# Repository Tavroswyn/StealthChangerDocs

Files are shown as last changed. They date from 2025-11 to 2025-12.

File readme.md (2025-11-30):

# DraftShift Documentation Source

This repository contains the source code for the DraftShift documentation website.

Visit [https://draftshift.github.io/Docs](https://draftshift.github.io/Docs) for the actual documentation.

---

## Contributing

We welcome contributions! If you'd like to help improve the documentation:

- Submit a descriptive [pull request](https://docs.github.com/en/pull-requests/collaborating-with-pull-requests/proposing-changes-to-your-work-with-pull-requests/creating-a-pull-request) of the feature/issue you are addressing.

- Keep the documented information concise.

### Contributing Build Guides

If you want to contribute build guides, please refer to the [Build Guide documentation](CONTRIBUTING_GUIDES.md) for more information.

### Development Setup

To run the documentation site locally:

1. **Prerequisites**: Ensure Python is installed and included in your environment PATH.

2. **Install dependencies**:
   ```
   pip install -r requirements.txt
   ```

3. **Run the development server**:
   ```
   python -m mkdocs serve
   ```

The site will be available at `http://127.0.0.1:8000` with live reload enabled.

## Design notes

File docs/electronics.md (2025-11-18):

---
search:
  boost: 2 
---

{%- macro set_io_display(io) -%}
<span style="text-align: left;">
{%- if io is mapping -%}
{%- for key, value in io.items() -%}
<div>{{ key }}: {{ value }}</div>
{%- endfor -%}
{%- else -%}
No
{%- endif -%}
</span>
{%- endmacro -%}

{% set board_data = {} %}

## Power Requirements
Adding more tools increases the power draw. The required wattage for your build will need to be calculated depending on the chosen hardware for each tool by the end user. 

!!! info "Wattage Calculation"
    See the following example of how one could calculate the wattage required for 6 tool heads.

    - Printing heater max output = `70W`
    - Printing fans - 3 total = `(0.1A * 3 fans) * 24V = 7.2W`
    - Resting heater output (30% of max for 5 tools) = `((70W / 100) * 30) * 5 tools = 105W`
    - Resting fans - 5 tools - `(0.1A * 24V) * 5 tools = 12W`
    - Extruder motors - 0.6A for 6 tools - `(0.6A * 24V) * 6 tools = 86W`

    6 tools with a 70w heater has resulted in `280W` total. This greatly exceeds the standard Voron 200W power supply without taking the rest of the system in to account and either an additional power supply is required to make up the difference or the standard power supply needs to be replaced with a larger wattage supply.

!!! danger "Unsure?"
    If you are unsure of your power requirements please reach out for help from the community via one of the social platforms. 

## Toolhead Boards
Each tool requires a toolhead board to go with it. With multiple tools, the wiring would become a nightmare to manage without them. See the below table for a list of boards and their features.

| Board | Image | Manufacturer | Protocol | Fan Outputs | Fan Voltage | Thermistor | RGB | Probe | Filament Sensor |
| :-: | :-: | :-: | :-: | :-: | :-: | :-: | :-: | :-: | :-: |
{% for manufacturer, boards in tool_boards.manufacturers.items() -%}
{% for board_key, data in boards.items() -%}
{% if data.features is defined -%}
{%- set target_attr = '' if data.external_link else '{: target="_blank"}' -%}
| [{{data.name}}]({{data.product_url}}){{target_attr}} | <span style="width: 100px; display: block;">{{data.name}}</span> | {{ manufacturer }} | {{ data.features.protocol }} | {{ data.features.fans|string }} | {{ data.features.fan_voltage }} | {{ data.features.thermistor|string }} | {{ data.features.rgb|string }} | {{ data.features.probe|string }} | {{ data.features.filament_sensor|string }} | 
{% endif -%}
{%- endfor -%}
{%- endfor %}

## Distribution Boards
Distribution boards extend the amount of connections available that can be used to attach tool heads. They will be either extend your CAN network or will behave as a USB hub. Some boards also have an additional MCU that gan give you access to additional runout switches, thermistors, RGB, etc.

See below table of known boards for their protocol and capability:
!!! danger "TODO"
    Add images

| Board |  | Protocol | Outputs | IO |
| :-: | :-: | :-: | :-: | :-: |
{% for manufacturer, boards in distribution_boards.manufacturers.items() -%}
{%- for board_key, data in boards.items() -%}
{%- if data.features is defined -%}
{%- set target_attr = '' if data.external_link else '{: target="_blank"}' -%}
| [{{data.name}}]({{data.product_url}}){{target_attr}} | <span style="width: 100px; display: block;">{{data.name}}</span> | {{data.features.protocol}} | {{data.features.outputs}} | {{set_io_display(data.features.IO)}} | 
{% endif -%}
{%- endfor -%}
{%- endfor %}

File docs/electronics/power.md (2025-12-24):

## Requirements
Every toolchanger build is different, the end user must calculate the required power budget based on the specific hardware selected for each toolhead. This includes considering peak loads, simultaneous heating, and any auxiliary accessories. Ensuring that the power supply is sized with adequate overhead prevents instability and brownouts.

!!! example "Wattage Calculation"
    The following calculations are theoretical and are provided only as an example of how one might estimate the power requirements for a 6 tool build. Actual values may vary depending on the specific components, settings, and operating conditions of your build.

    - Toolheads - Active heater at max output = `70W`
    - Toolheads - Resting heater output (30% of max for 5 tools) = `((70W / 100) * 30) * 5 tools = 105W`
    - Toolheads - Active part cooling fans - 2 total = `(0.1A * 2 fans) * 24V = 4.8W`
    - Toolheads - Active hotend fans - 6 total = `(0.1A * 6 fans) * 24V = 14.4W`
    - Toolheads - Extruder motors - 0.6A for 6 tools - `(0.6A * 24V) * 6 tools = 86W`
    - Toolheads - combined total = `280,2W`  

    - Printer baseline = `120W`
    - Combined total = `400,2W`

In this example, 6 toolheads equipped with 70W heaters produce a combined load of 280W@24V. This alone exceeds the standard Voron 200W-24V power supply before accounting for motion stepper motors, electronics, fans, and other system components which would typically consume around 100-120W@24V.

So be safe and choose an adequately rated PSU for your expected current consumption.

!!! warning "Current Draw Baseline and Spikes"
    A standard Voron v2 draws somewhere in the 50-120w range "just sitting there" with all heaters and fans off, make sure you account for your baseline and spikes when you run the numbers for your power consumption.

!!! warning "DC Beds"
    A typical Voron has an AC bed, which does not draw power from the printer's PSU. If you have a DC bed, you will need to include that in your power calculations and spec the PSU accordingly.

In practice, this means that either an [additional power supply](#additional-power-supplies) would be required to cover the extra demand, or the stock supply must be [replaced with a higher-wattage unit](#replacement-power-supplies). These figures are illustrative; your actual power requirements will depend on the specific hardware and configuration of your build.

!!! danger "Unsure?"
    If you are unsure of your power requirements please reach out for help from the community via one of the social platforms. 

## Additional Power Supplies
A common method for increasing available power capacity is to add a second power supply unit (PSU) to the printer. While this approach is straightforward, it comes with both advantages and trade-offs:

- **Cost-effective:** Allows you to retain your existing PSU and supplement only the additional power required.
- **Increased space requirements:** A second PSU occupies additional room within the electronics bay.
- **Additional wiring complexity:** Integrating multiple PSUs introduces more wiring and requires careful planning to ensure safe, reliable operation.

!!! info "Common Ground"
    In multi-PSU systems, it is recommended to connect the negative (ground) rails together. This prevents floating grounds, which can lead to communication issues, inconsistent sensor readings, and other electrical irregularities.

!!! tip "48 Volt"
    If you’re adding another power supply and your motor drivers support it, incorporating a 48 V PSU can improve motion performance—particularly for Z-axis travel. Higher voltage reduces motor torque loss at speed, enabling faster and more responsive movement. Moving the load from all the motors to the 48V power supply frees up some capacity on the 24V power supply.

    Ultimately, upgrading to 48 V motion can shorten tool-change times and may be a worthwhile improvement depending on your hardware capabilities and performance goals.

## Replacement Power Supplies
Replacing your existing power supply unit (PSU) offers the inverse set of trade-offs compared to adding an [additional PSU](#additional-power-supplies). While it is generally the more expensive option, a single higher-capacity PSU can free up space in the electronics bay and reduce overall wiring complexity. Someone seeking a cleaner, more streamlined setup and prefers to avoid managing multiple power sources, a full PSU replacement may be the more appealing path.

## Power Supply Options
See the below table for some of the more common power supply unit (PSU) options. All PSUs are available in 24V and 48V options, unless noted otherwise.

{% for mf in power_supplies %}
### {{ mf }}
| Model | Wattage | Dimensions |
| :-: | :-: | :-: |
{%- for model, data in power_supplies[mf].items() %}
| {{ model }} | {{ data.wattage }} | {{ data.dimensions|join(", ") }}mm |
{%- endfor %}
{% endfor %}

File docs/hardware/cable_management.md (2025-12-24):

---
search:
  boost: 2 
---

## Umbilical Cables
An umbilical cable is required for each toolhead. It consists of a PTFE tube that feeds the filament to the toolhead's extruder, and an electrical wire that transfers power and data from the [distribution board](../electronics/distro_boards.md) to a [toolhead board](../electronics/th_boards.md). On a StealthChanger, keeping the tool's umbilical in a controlled state is extremely important. If a tool's umbilical were to obstruct any of the other tools, it could result in a crash and cause a print failure.

To help the umbilical move in a controlled fashion, we employ the use of a flat spring steel or piano wire. This addition gives the umbilical a controlled arc and helps it return to its resting position safely.

!!! tip "Spring Steel?"
    Flat spring steel (3x0.3mm) is the preferred aid for the tool's umbilical. It provides better lateral control and is what comes supplied as part of the LDO `Toolhead and Dock Kit`.

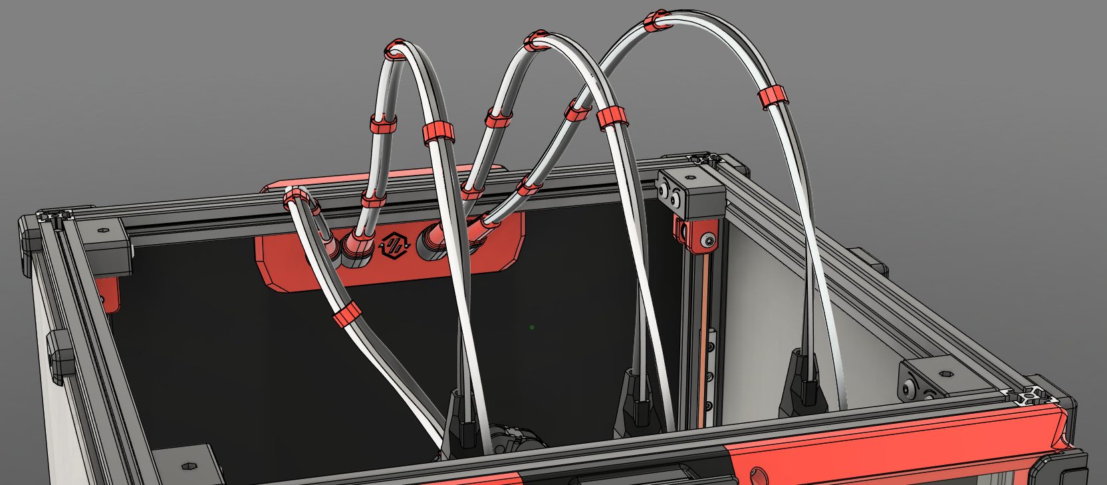
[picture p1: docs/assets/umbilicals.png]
Umbilical Cables


## Fanny Pack
Originally by [ManCheetah](https://www.printables.com/@EddieSha_454383){:target="_blank"}, the Fanny Pack has been adopted by DraftShift Design as the de facto method of housing a [distribution board](../electronics/distro_boards.md) on the rear of the printer. Compared to the original, our updated version brings compatibility with a number of [distribution boards](../electronics/distro_boards.md) and buck converter options.

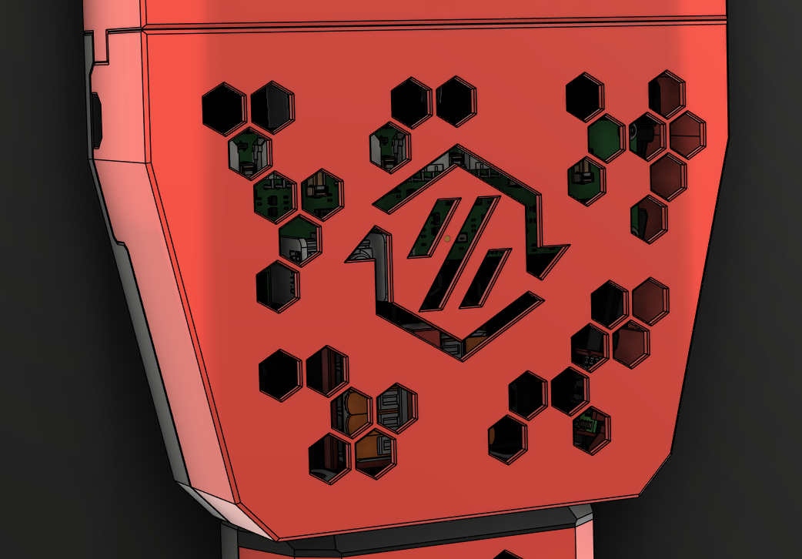
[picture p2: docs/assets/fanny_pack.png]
Fanny Pack


## Wire Duct
The Wire Duct serves as a conduit between the [Fanny Pack](#fanny-pack) and your printers electronics bay. Under its cover is an EMS compatible panel for you to mount any extra pieces you might need. 

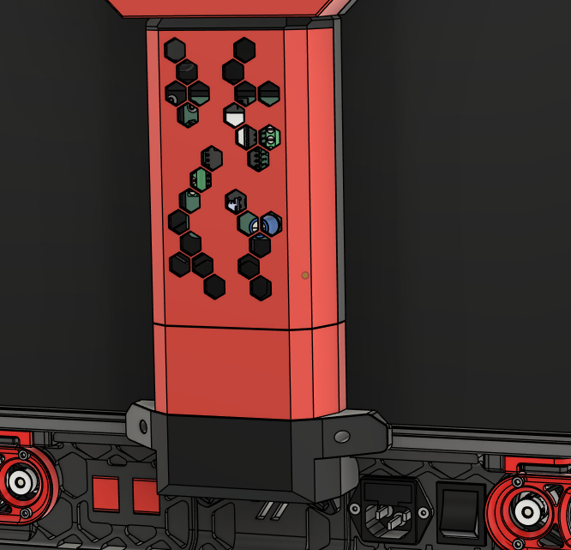
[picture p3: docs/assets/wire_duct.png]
Wire Duct


## Assembly
See the [Build Guides](../hardware/guides/cable_management/index.md) for assembly instructions.

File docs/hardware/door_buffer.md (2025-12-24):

---
search:
  boost: 2 
---

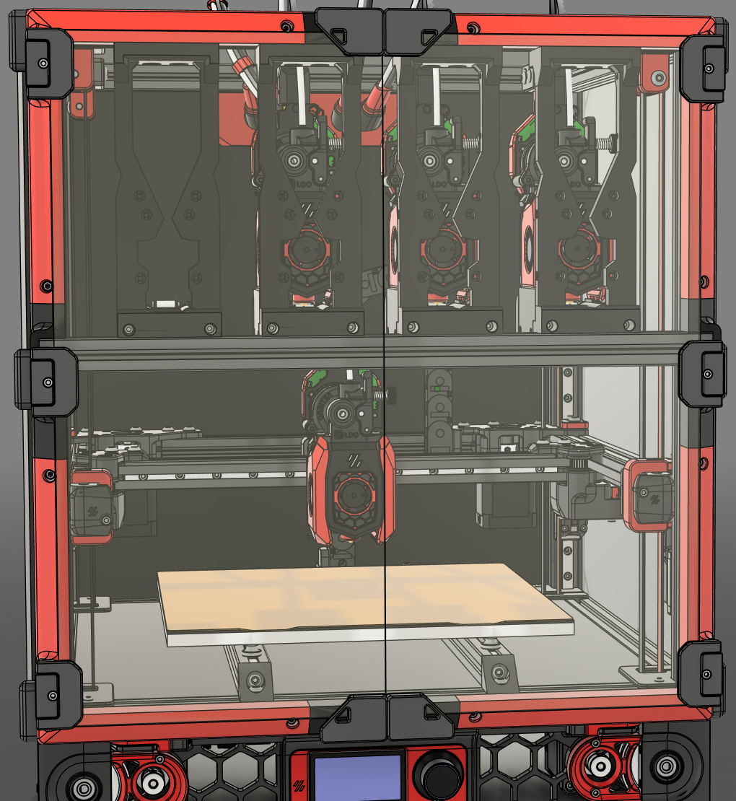
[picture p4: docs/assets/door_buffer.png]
Door Buffer


## Context

### The Problem
To give the [Modular Docks](modular_dock.md) the maximum amount of rigidity, they need to be supported above and below. Adding an extrusion [crossbar](#crossbar) solves that problem but also introduces another. With the crossbar in line with the frame, the standard Voron V2 front-idlers collide with the crossbar and moving the extrusion outside of the frame would get in the way of mounting the door.

Idler interference

### The Solution
Adding a Door Buffer provides a means to install the [crossbar](#crossbar) and retain the ability to mount the door on the front. The Door Buffer uses 3D printed pieces to fill the gaps around the front of the printers frame and adds new mounting points for the door.

Door buffer solution

There are versions of the Door Buffer for both [standard Voron V2 doors](https://github.com/DraftShift/DoorBuffer/tree/main/STL/Stock%20Voron){:target="_blank"} and the [ClickyClack Fridge Door Mod](https://github.com/DraftShift/DoorBuffer/tree/main/STL/Clicky-Klack){:target="_blank"}, as well as options for [Micron](https://github.com/DraftShift/DoorBuffer/tree/main/STL/Micron){:target="_blank"}.

!!! info "Alternatives"
    You don't necessarily need to use printed pieces to act as a buffer. There are some other methods that the community uses.

    * **2020/1515 Extrusion** - Using blind joints you can mount extrusion to the front of the frame essentially making it 4020/3015.
    * **4020/3015 Extrusion** - Build the front of your printers frame using larger extrusion. 
    * **Mini/Micro BFI** - [Mini/Micro BFI](https://github.com/DraftShift/StealthChanger/tree/main/UserMods/BT123/MiniBFI%20%2B%20MicroBFI){:target="_blank"} takes a different approach and shortens the BFI idlers. This means the [crossbar](#crossbar) can be kept within the printers frame at the cost of less printable area and reduces the amount you can adjust the A/B belts.

## Crossbar
The crossbar is a piece of extrusion mounted to the front of the printer’s frame, providing a rigid and stable attachment point for the bottom of the [Modular Dock](modular_dock.md).

The crossbar should be made from extrusion that matches your printer, 2020 for Voron V2 or 1515 for Micron. The length of the crossbar changes depending on the size of your frame and which version of Door Buffer you are using.

| Printer | DraftShift Crossbar | LDO Crossbar |
| --- | --- | --- |
| Voron 250 | 400mm | 370mm |
| Voron 300 | 450mm | 420mm |
| Voron 350 | 500mm | 470mm |
| Micron 180 | 302mm | - |

!!! tip "Crossbar Adapter"
    You can use the DraftShift Door Buffer with LDO length extrusions by using an [adapter](https://github.com/DraftShift/DoorBuffer/tree/main/STL/Adaptor){:target="_blank"}.

!!! info "Monolith AWD"
    With Monolith protrusion the front motors would hit the crossbar even with the door-buffer. To work around that you can use one of the following usermods:

    - [printed adapter for door buffer with crossbar and Monolith AWD](https://github.com/DraftShift/DoorBuffer/tree/main/UserMods/MikeYankeeOscarBeta/Doorbuffer_Adapters){:target="_blank"}
    
    - [printed adapter for crossbar with doomcube 4040 frame and Monolith AWD](https://github.com/DraftShift/ModularDock/tree/main/UserMods/MikeYankeeOscarBeta/Monolith_Crossbar){:target="_blank"}

## Assembly
The assembly guide for the Door Buffer can be found in the [Build Guides](guides/door_buffers/index.md) section.

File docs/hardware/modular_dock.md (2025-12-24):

---
search:
  boost: 2 
---

The Modular Dock gives you a place to rest the tools while they are not in use. Its modular design allows for flexible configurations to suit any printer and toolhead combination.

## Application
The Modular Dock can be used in a variety of ways. The most common and recommended way is to use it in combination with a [crossbar](door_buffer.md#crossbar). The [crossbar](door_buffer.md#crossbar) is a part of the [Door Buffer](door_buffer.md) and offers a sturdy mounting point for the dock to be supported both above by the frame and below by the [crossbar](door_buffer.md#crossbar).

Alternatively, the dock can be mounted to the printer's frame using the [Stabilizers](#stabilizers) and [Link](#links) components. This keeps the lower portion of the docks in place by joining them together while the outer docks get supported by the side of the printers frame. This adds some rigidity, but will not provide the same level of stability as the [crossbar](door_buffer.md#crossbar).

Finally, the docks can be hung from the top of the printers frame with no lower support. This is the least stable option and should only used when the other options are not available to you. If you choose to go for top-mounted docks it's recommended to mount extra corner brackets to avoid the top-extrusion twisting around the blind joints.

## Modularity
Because of its modularity, the Modular Dock has many differing pieces that can become overwhelming rather quickly. To help navigate the options, the modular dock is broken down into the following subcomponents:

* [Base](#base) - The section that the tool rests on while docked.
* [Blocker](#blocker) - A section that mounts inside the [base](#base) and blocks the nozzle while docked, helping with ooze control.
* [Back](#back) - Attaches to the rear of the [base](#base) to allow adjustment of the tools resting position.
* [Wiper](#wiper) - A means of wiping the nozzle as the toolhead is exiting the dock.
* [Frame](#frame) - The upright portion of the dock that connects to the top of the printer's frame and optionally a [crossbar](door_buffer.md#crossbar).
* [Links](#links) - Attaches to the bottom of the docks, increasing rigidity for hanging docks.
* [Stabilizers](#stabilizers) - Ties the docks in to the side of the frame, further increasing rigidity for hanging docks.
* [Containers](#containers) - An optional addon that add a bit of flair to the front of the dock.

## Components
### Base
The base is a large section that is toolhead specific which has been shaped to match the bottom of the toolhead. It defines the width of the dock and helps define the position that the tool sits in on the Y Axis. The base can be availiable in 2 variants, `standard` and `stubby`. Every toolhead has a `standard` base, but not all toolheads have the smaller `stubby` base.

!!! warning "Smaller is better right?"
    The `stubby` base is **NOT** compatible when using a [Door Buffer](door_buffer.md). If you are using a [Door Buffer](door_buffer.md), you MUST use the `standard` base. 

| Base - Standard | Base - Stubby |
| :-: | :-: |
| Standard | Stubby |

### Blocker
The Blocker is a section that is toolhead agnostic and mounts inside the [Base](#base). It serves as a barrier to prevent ooze while the tool is docked. It is availiable in 2 variants, `cup` and `spring steel`. 

There is no real advantage using one over the other, its more about what you have available to you.

The `cup` version uses a pen spring, screw and heatset insert, while the `spring steel` version uses a strip of flat spring steel. Both versions use high temperature RTV silicone to block the nozzle.

!!! tip "LDO Toolhead and Dock Kit"
    The LDO Toolhead and Dock Kit includes pre moulded `spring steel` blockers. If you are using the LDO kit, you will need to print the `spring steel` variant.

| Blocker - Cup | Blocker - Spring Steel |
| :-: | :-: |
| Cup | Spring Steel |

### Back
The Back plate is toolhead specific and bolts to the rear of the [Base](#base). Adjusting it up or down can help maintain the tool's alignment while it is docked.

| Back |
| :-: |
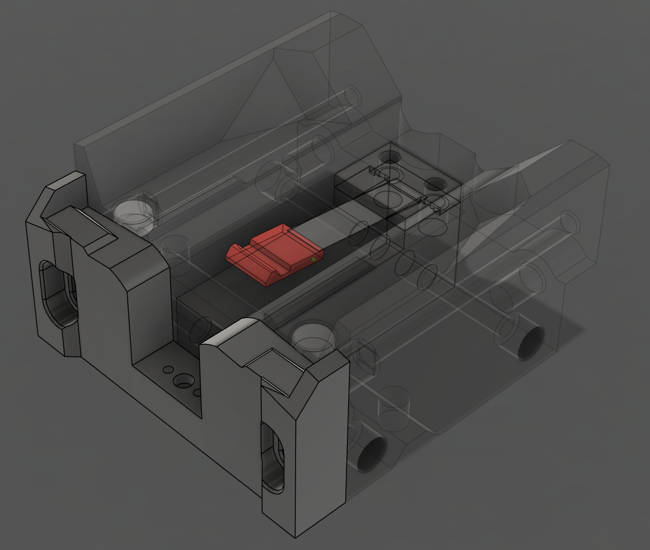
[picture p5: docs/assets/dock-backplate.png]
Back
|  |

### Wiper
The Wiper is toolhead agnostic and mounts to the [Back](#back) plate. There are 2 variants, `ptfe` and `bambu`. Both use a piece of PTFE tube to wipe the nozzle as it exits the dock. The `bambu` version emulates the wiper from the P1/X1 series of printers and can be printed or purchased from [BambuLab](https://bambulab.com){:target="_blank"}.

!!! tip "Wipers Are Considered Optional"
    If you get excess ooze while returning to the print, a wiper may help.

| Wiper - PTFE | Wiper - Bambu |
| :-: | :-: |
| PTFE | Bambu | -->

### Frame
The Modular Dock Frame can be considered to be the front of the dock. It consists of left, right, top and bottom pieces. 

The left and right pieces come in 2 variants, `standard` and `short`. This determines the height of the dock. 

!!! warning "Short Frame Saves More Space?"
    Using the `short` version of the Frame can give you more printable area under the bed, but it does have some caveats. 

    * You may need to adjust the position of the z rails to ensure the carriage can reach.
    * [StealthBurner](toolheads.md#stealthburner) is not compatible with short docks.
    * [Containers](#containers) are not compatible with short docks.

Versions of both the top and bottom pieces are available for 1515 and 2020 extrusions. Both of those versions have 2 variants, `standard` and `crossbar`. The `crossbar` versions are used in combination with [Door Buffer](door_buffer.md), which mounts an extrusion outside of the frame as a crossbar. The `standard` versions can be used for a crossbar in-line with the frame, as a combination with [Stabilizers](#stabilizers) or when hanging from the top of the printers frame. Optionally there is also an 'L bracket' that can help with stability of hanging docks.

| Standard Height | Short Height |
| :-: | :-: |
| Standard-Standard | Short-Standard |

### Links
Links can be used to tie the frame and base of the docks together to gain more rigidity for hanging docks or when using [Stabilizers](#stabilizers). There are seperate links pieces for the [Frame](#frame) and the [Base](#base).

The links for the [Frame](#frame) differ depending on whether 2020 or 1515 top and bottom pieces are used and whether the dock is for a wider tool or not. The links for the [Base](#base) are the same no matter the configuration.

| Links |
| :-: |
| Links |

### Stabilizers
Stabilizers can be added to the first and last dock to help with rigidity for hanging docks. There are left and right brackets for 2020 and 1515 frames which mount on the top Y axis extrusions of the printer's frame, spacers and a brace which connects to the outer docks.

!!! tip "Think ahead"
    * There are different versions of the brace depending on the combination of pieces chosen to build the dock. Make sure to get the correct version.
    * The spacers can be scaled in the slicer to adjust the offset of the docks from the side of the printer. These should be printed last, giving you a change to measure the distance you require.

| Stabilizers |
| :-: |
| Stabilizer |

### Containers
Containers are an aesthetic addon that can be position in the frame of the Modular Dock. They are considered optional.

| Containers |
| :-: |
| Containers |

## Assembly
The assembly guide for the Modular Dock can be found in the [Build Guides](guides/modular_docks/index.md) section. There you will find a guide for the different components and how to contruct the final assembly.

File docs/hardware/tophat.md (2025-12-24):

---
search:
  boost: 2 
---

## The Problem
While the tools are parked or when printing high up, the umbilical extends past the top of the printer. Most printers let the umbilical touch the top or go to the side. That is not an option for StealthChanger, the umbilical would interfere with other tools or their umbilical and could pull them from their dock. 

## The Solutions

### Extrusion Tophat
The Extrusion Tophat is like an extension of your printer. It uses the same extrusion and panel design as the printers frame. See the below table for a list of extrusion and panel sizes per printer size:

| Printer | Vertical Extrusion | Horizontal Extrusion | Panels |
| :-: | :-: | :-: | :-: |
| Voron 350 | 250mm x4 | 470mm x8 | 483x223x3mm x4 |
| Voron 300 | 200mm x4 | 420mm x8 | 433x173x3mm x4 |
| Voron 250 | 200mm x4 | 370mm x8 | 383x173x3mm x4 |
| Micron 180 | 150mm x4 | 280mm x8 | 290x130x3mm x4 |

Extrusion Tophat

!!! tip "LDO Kit"
    The hardware required for the Extrusion Tophat comes as part of LDO's `Tophat and Door Buffer Kit`.

### Printed Tophat
The Printed Tophat was developed for users that do not have easy access to aluminium extrusion or acrylic panels. The only additional hardware is screws, nuts and heat-set inserts.

Printed Tophat

!!! tip "Interim Tophat"
    Many of our members have fabricated a Tophat from cardboard which can be used while printing the pieces for your Printed Tophat.

### Do Nothing
If you plan on only printing open air, then you do not necessarily require a Tophat. You could just remove the top panel and let the umbilical cables extend past the top of the printer. 

## Assembly
The assembly guides for the Tophats can be found in the [Build Guides](guides/tophats/index.md) section.

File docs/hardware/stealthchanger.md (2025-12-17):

---
search:
  boost: 2 
---

StealthChanger is the key component and namesake of the StealthChanger ecosystem. It can be broken down in to 2 main components, the [Shuttle](#shuttle) and [Backplate](#backplate), which allows the toolhead to be removed from the gantry and be docked so that another tool can be picked up. During operation, the mechanism also behaves like [Voron Tap](https://github.com/VoronDesign/Voron-Tap){:target="_blank"} and can be used for probing the bed. The [Shuttle](#shuttle) and [Backplate](#backplate) completely replace Voron TAP hardware, only the optoTAP sensor is re-used.

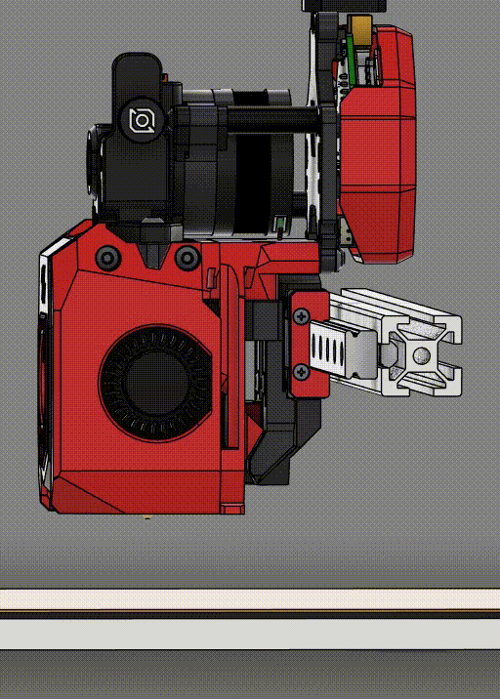
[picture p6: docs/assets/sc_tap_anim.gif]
StealthChanger
StealthChanger 

## Shuttle
The StealthChanger Shuttle gets mounted to the gantry's X-rail MGN carriage and serves the purpose of being a receptacle for the [Backplate](#backplate). It uses bushings and magnets which allow the [Backplate](#backplate) to
kinematically attach to the gantry.

### Printed vs CNC
The printed and CNC versions of the Shuttle both operate in the same way. You can print the shuttle and source the bushings, magnet and screws or purchase a ready to go CNC shuttle. 

CNC Shuttles offer some QOL improvements like improved belt retention and in the case of LDO's Shuttle, precision-machined bushings.

When printing a Shuttle, it is important to note that the selection of material you use and your printers accuracy are important. Please reference the [Print Tuning Section](../getting_started.md#print-tuning) before printing your Shuttle.

!!! warning "ABS+"
    We have found that when used for StealthChanger, ABS+ tends to crack over time and advise against using it.

Shuttles

| Shuttle | MGN12 | MGN9 | Micron | 6mm Belt | 9mm Belt |
| :-: | :-: | :-: | :-: | :-: | :-: |
| Printed | :fontawesome-solid-check:{style="color:green;"} | :fontawesome-solid-asterisk:{style="color:orange;"} | :fontawesome-solid-asterisk:{style="color:orange;"} | :fontawesome-solid-check:{style="color:green;"} | :fontawesome-solid-asterisk:{style="color:orange;"} |
| CNC | :fontawesome-solid-check:{style="color:green;"} | :fontawesome-solid-xmark:{style="color:red;"} | :fontawesome-solid-xmark:{style="color:red;"} | :fontawesome-solid-check:{style="color:green;"} | :fontawesome-solid-check:{style="color:green;"} |

!!! asterisk "MGN9/Micron"
    The hole spacing on MGN9 is too small to clamp the belts reliably without the screws getting in the way. This means a Voron V2 with MGN9 on X axis or a Micron requires the use of the [Shuttle Keeper](#shuttle-keeper). 

!!! asterisk "9mm belts"
    9mm belts can be used with CNC Shuttles. If you want to use 9mm belts with a printed Shuttle, a [usermod by BT123](https://github.com/DraftShift/StealthChanger/tree/main/UserMods/BT123/Split%20Keeper){:target="_blank"} is required.

!!! info "Monolith and Inverted Belts"
    Inverted belts with printed shuttle require the use of this [usermod by BT123](https://github.com/DraftShift/StealthChanger/tree/main/UserMods/BT123/Split%20Keeper){:target="_blank"}.
    Inverted belts can be mounted to CNC Shuttle as is, but with [Monolith](https://github.com/Monolith3D/Monolith_Gantry/tree/main){target="_blank"} this results in slight angled belt-path. To get a straight belt path with CNC-shuttle you can either use [belt-lock](https://github.com/MikeYankeeOscarBeta/belt_lock){:target="_blank"} or this [XY-joint mod by dderg](https://github.com/Monolith3D/Monolith_Gantry/tree/main/UserMods/dderg/XY%20Joints%20compatible%20with%20Fysetc%20CNC%20Stealthchanger%20Shuttle){:target="_blank"}.

## Shuttle Keeper
The Shuttle Keeper is an additional component that can be used to hold the belts in place while the [Shuttle](#shuttle) is removed from the MGN Rail. There are situational reasons as to when and why you would want to use a Shuttle Keeper. See the below list for details.

* Only compatible with a printed [Shuttle](#shuttle).
* Required for a MGN9 [Shuttle](#shuttle).
* Optional for a MGN12 [Shuttle](#shuttle).
* Shuttle Keeper moves the toolhead forward 5-6mm.

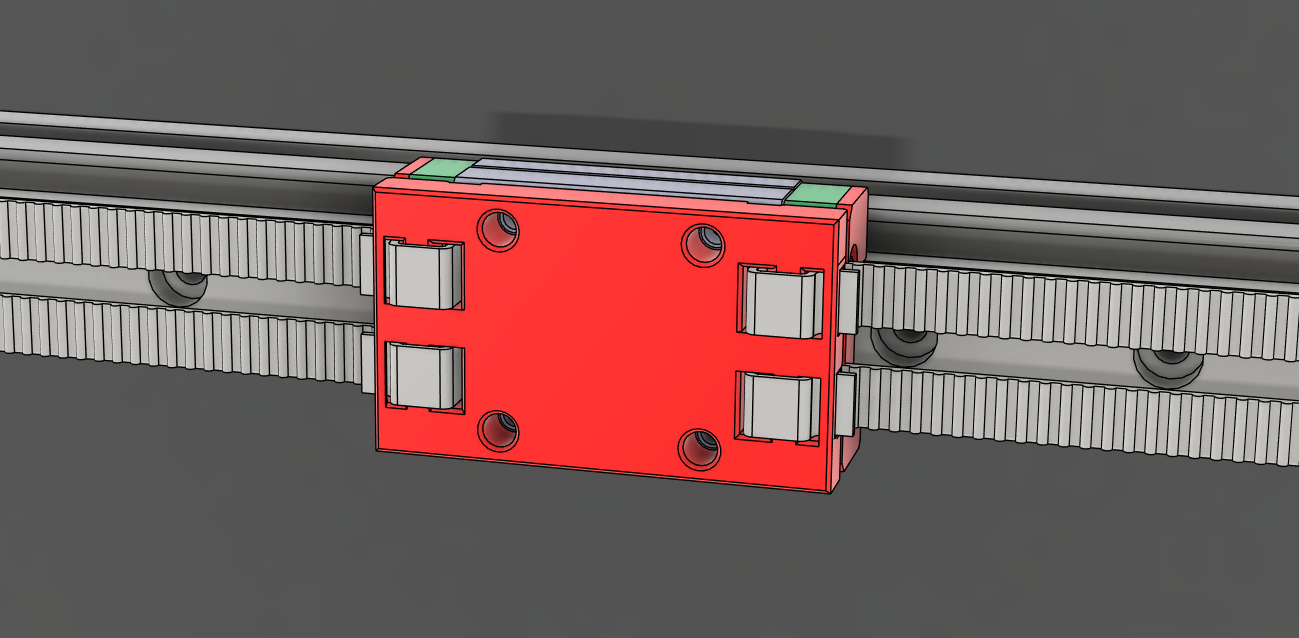
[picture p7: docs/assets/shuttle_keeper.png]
Shuttle Keeper


## Belt Helper
Belt helper is a tool that will hold your belts for you while installing the [Shuttle](#shuttle). Once attached to the belts, the Belt Helper will assist in pulling the belts into position for the [Shuttle](#shuttle) to clamp them.

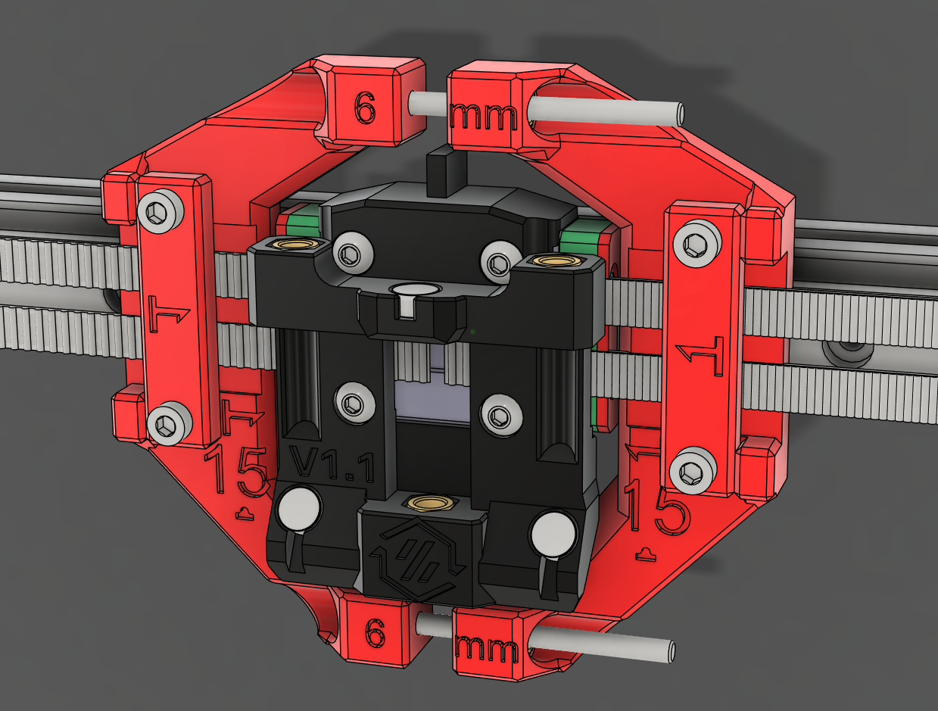
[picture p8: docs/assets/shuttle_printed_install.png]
Shuttle Install


!!! tip "One Tool to Rule Them All"
    The Belt Helper was designed to assist with installing the printed [Shuttle](#shuttle). It can also be useful with CNC shuttles to give you that extra set of hands you always wanted.

!!! info "Mini/Micro BFI"
    If using [Mini/Micro BFI](https://github.com/DraftShift/StealthChanger/tree/main/UserMods/BT123/MiniBFI%20%2B%20MicroBFI){:target="_blank"}, the Belt Helper is required to pre tension your belts to a point where your idlers only need minimal adjustment.

## Backplate
The StealthChanger Backplate is the companion component to the [Shuttle](#shuttle). Each compatible toolhead has its own unique Backplate that gets attached to the tool. The backplate is a critical component of StealthChanger and requires you to ensure you have good print accuracy, especially when pairing with a CNC Shuttle. Please reference the [Print Tuning Section](../getting_started.md#print-tuning) before printing your Backplate. For a list of compatible tools, see the [Toolheads](toolheads.md) page.

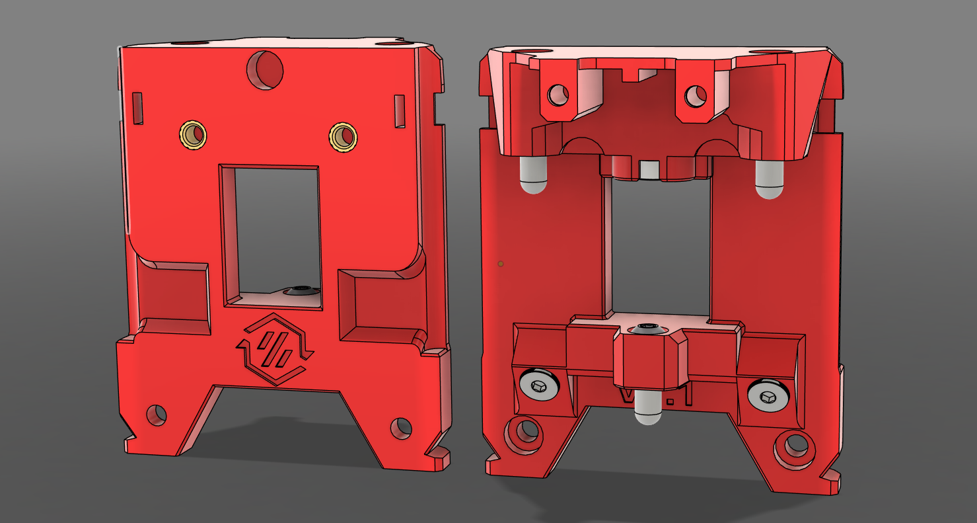
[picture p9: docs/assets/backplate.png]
Backplate


## Assembly
See the [Shuttle Build Guides](guides/shuttles/index.md) and [Backplate Build Guides](guides/backplates/index.md) sections for assembly instructions.

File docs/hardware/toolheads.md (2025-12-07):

For the purposes of StealthChanger the toolhead selection is rather important. It is often the deciding factor in how the rest of the build is configured. It determines which docks you can use, the maximum number of tools you can use, and can also have a large impact on power requirements.

???+ info "Printing"
    Officially supported toolheads require no modifications to operate with StealthChanger beyond the installation of the StealthChanger backplate and, where applicable, a spacer. Each toolhead can be sourced from their respective repositories. 
    
    Toolheads that require modification to work with StealthChanger are not officially supported and should be submitted as a usermod.

??? info "Extruders"
    * You can use any extruder you want as long as it is supported by the toolhead of your choice.
    * It's important to note that the width of the extruder may impact the maximum tool count as it may require a wider dock, limiting the total number of tools that can be accommodated.
    * :warning: Pay attention to the tensioning screw on the extruder, it may collide with the tool beside it if it extends outside the tool's width and there is not enough room between them.

??? info "Hotends"
    * Choose whichever hotend you like, as long as the toolhead supports it, you can use it.
    * :warning: Some high-flow hotends may require significant tuning to prevent oozing while moving to and from the dock.

??? tip "Community Recommendation"
    [Anthead](#anthead) is the recommended toolhead due to its integrated magnets in the fan ducts, which enhance stability during the docking process. Other tools can achieve similar results, but may require additional modifications.

    The LDO `Toolhead and Dock Kit` includes all necessary hardware for the [Anthead](#anthead), with the exception of the extruder and hotend components.

<div class="grid cards" style="text-align: center;" markdown>

{% for tool, tool_data in tools.toolheads.items() %}
    {% set v250 = tools.max_tools[tool_data.dock_width][250]|string if tools.max_tools[tool_data.dock_width][250] > 0  else '-' %}
    {% set v300 = tools.max_tools[tool_data.dock_width][300]|string if tools.max_tools[tool_data.dock_width][300] > 0  else '-' %}
    {% set v350 = tools.max_tools[tool_data.dock_width][350]|string if tools.max_tools[tool_data.dock_width][350] > 0  else '-' %}
    {% set m180 = tools.max_tools[tool_data.dock_width][180]|string if tools.max_tools[tool_data.dock_width][180] > 0  else '-' %}
-   <span id="{{ tool.replace(' ', '_').lower() }}"></span>

    ### {{ tool }}

    {{ tool }}

    **Author:** {{ tool_data.author }}

    **Dock Width:**{ title="Standard: 60mm<br>Wide: 76mm" } {{ tool_data.dock_width.capitalize() }}

    **Short Dock:**{ title="The height of the dock (Z axis) being less than standard. For Voron printers, the shorter height is not available for larger toolheads. Compatibility with Door Buffer varies depending on toolhead configuration. For Micron printers the short variant is a requirement." } {{ ':fontawesome-solid-check:{ style="color:green;" }' if tool_data.short_dock else ':fontawesome-solid-xmark:{ style="color:red;" }' }}

    **Stubby Dock:**{ title="The depth of the dock (Y axis) being less than standard and is not compatible with Door Buffer and is only available for the smaller toolheads." } {{ ':fontawesome-solid-check:{ style="color:green;" }' if tool_data.stubby_dock else ':fontawesome-solid-xmark:{ style="color:red;" }' }}

    {% if tool_data.extra is defined %}
    {% for extra in tool_data.extra %}
    {{ extra }}<br>
    {% endfor %}
    {% endif %}

    | Size | Max Tools |
    |--------------|------------|
    | 250mm Voron  | {{ v250 }} |
    | 300mm Voron  | {{ v300 }} |
    | 350mm Voron  | {{ v350 }} |
    | 180mm Micron | {{ m180 }} |

    [:fontawesome-brands-github: View on GitHub]({{ tool_data.url }}){:target="_blank" .md-button}

{% endfor %}

</div>

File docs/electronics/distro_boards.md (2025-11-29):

{%- macro set_io_display(io) -%}
{%- if io is mapping -%}
{% for key, value in io.items() %}
    **{{ key }}:** {{ value }}
{% endfor %}
{%- endif -%}
{%- endmacro -%}

Distribution boards expand the number of connections available for attaching toolheads. They can either extend your CAN network or function as a USB hub. Some distribution boards also include an additional MCU, providing access to extra inputs and outputs such as filament runout switches, thermistors, RGB lighting, and other peripherals.

??? tip "CAN Bus"
    For CAN bus communication, it is highly recommended to follow [Esoterical's CAN Bus Guide](https://canbus.esoterical.online/){target="_blank"}, which provides clear, step-by-step instructions for flashing and configuring the host computer, MCU and toolhead boards.

??? tip "USB"
    For USB communication it is recommended to use the manufacturer's documentation to guide you through flashing and configuring the distribution board.

<div class="grid cards" style="text-align: center;" markdown>
{% for manufacturer, boards in distribution_boards.manufacturers.items() %}
    {% for board, data in boards.items() %}
    {% if data.features is defined %}
    {% set target_attr = "_blank" if data.external_link else "" %}
-    ## {{ board }}
    
    {{ board }}
    
    **Manufacturer:** {{ manufacturer }}
    
    **Protocol:** {{ data.features.protocol }}
    
    **Outputs:** {{ data.features.outputs }}
    
    {{ set_io_display(data.features.IO) }}
    
    [:octicons-info-16:More Info]({{ data.url }}){:target="_blank" .md-button .md-button--primary} [:material-cart:]({{ data.product_url }}){:target="{{ target_attr }}" .md-button}
    {% endif %}
    {% endfor %}
{% endfor %}
</div>

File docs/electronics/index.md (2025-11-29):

# Power and Electronics

Building a toolchanger inherently increases both the [power demand](power.md) and the amount of I/O the printer must support. Each toolhead typically needs its own heater, extruder, fans, and OptoTap PCB, which quickly makes direct wiring complex and unwieldy.

The most effective way to manage this is to use a [toolhead board](th_boards.md) on each tool, which keeps all of the tool’s wiring self-contained within the toolhead itself. Complementing this, [distribution boards](distro_boards.md) serve as centralized hubs that deliver both power and data to each toolhead board, typically over CAN bus or USB. Together, these boards simplify wiring, improve reliability, and make multi-tool systems far easier to build and maintain.

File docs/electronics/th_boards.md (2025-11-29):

Each toolhead in a multi-tool setup requires its own dedicated toolhead board. Without these boards, the wiring for heaters, sensors, fans, and motors would quickly become unmanageable as the number of tools increases. Toolhead boards consolidate all of a tool’s connections into a single, organized interface, preventing the wiring complexity from becoming overwhelming and greatly simplifying installation, maintenance, and troubleshooting.

??? tip "CAN Bus"
    For CAN bus communication, it is highly recommended to follow [Esoterical's CAN Bus Guide](https://canbus.esoterical.online/){target="_blank"}, which provides clear, step-by-step instructions for flashing and configuring the host computer, MCU and toolhead boards.

??? tip "USB"
    For USB communication it is recommended to use the manufacturer's documentation to guide you through flashing and configuring the toolhead boards.

<div class="grid cards" style="text-align: center;" markdown>
{% for manufacturer, boards in tool_boards.manufacturers.items() %}
    {% for board, data in boards.items() %}
    {% if data.features is defined %}
    {% set target_attr = "_blank" if data.external_link else "" %}
-    ## {{ board }}
    
    {{ board }}
    
    **Manufacturer:** {{ manufacturer }}

    **Protocol:** {{ data.features.protocol }}
    
    **Fan Outputs:** {{ data.features.fans|string }}
    
    **Fan Voltage:** {{ data.features.fan_voltage|string }}
    
    **Thermistor:** {{ data.features.thermistor|string }}
    
    **RGB:** {{ data.features.rgb|string }}
    
    **Probe:** {{ data.features.probe|string }}
    
    **Filament Sensor:** {{ data.features.filament_sensor|string }}
    
    [:fontawesome-solid-info-circle: More Info]({{ data.url }}){:target="_blank" .md-button .md-button--primary} [:material-cart:]({{ data.product_url }}){:target="{{ target_attr }}" .md-button}
    {% endif %}
    {% endfor %}
{% endfor %}
</div>

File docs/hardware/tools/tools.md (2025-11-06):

For the purposes of StealthChanger the toolhead selection is rather important. It is often the deciding factor in how the rest of the build is configured. It determines which docks you can use, the maximum number of tools you can use, and can also have a large impact on power requirements.

???+ info "Printing"
    Officially supported toolheads do not require modification to work with StealthChanger, only the addition of the Stealthchanger backplate and possibly a spacer. Each toolhead can be sourced from their respective repositories. Toolheads that are not officially supported will require modification to work with StealthChanger and will be marked as a usermod.

??? info "Extruders"
    * You can use any extruder you want as long as it is supported by the toolhead of your choice.
    * It's important to note that the width of the extruder may impact the maximum tool count as it may render the tool width wider, potentially limiting the total number of tools that can be accommodated.
    * :warning: Pay attention to the tensioning screw on the extruder, it may collide with the tool beside it if it extends outside the tool's width and there is not enough room between them.

??? info "Hotends"
    * Choose whichever hotend you like, as long as the toolhead supports it, you can use it.
    * :warning: Some high-flow hotends may require significant tuning to prevent oozing while moving to, and from the dock.

??? tip "Community Recommendation"
    Anthead is the recommended toolhead due to its integrated magnets in the fan ducts, which enhance stability during the docking process. Other tools can achieve similar results, but may require additional modifications.

<div class="grid cards" style="text-align: center;" markdown>

{% for tool, tool_data in toolheads.items() %}
    {% set v250 = max_tools[tool_data.dock_width][250]|string if max_tools[tool_data.dock_width][250] > 0  else '-' %}
    {% set v300 = max_tools[tool_data.dock_width][300]|string if max_tools[tool_data.dock_width][300] > 0  else '-' %}
    {% set v350 = max_tools[tool_data.dock_width][350]|string if max_tools[tool_data.dock_width][350] > 0  else '-' %}
    {% set m180 = max_tools[tool_data.dock_width][180]|string if max_tools[tool_data.dock_width][180] > 0  else '-' %}
-   <span id="{{ tool.replace(' ', '_').lower() }}"></span>

    ### {{ tool }}

    {{ tool }}

    **Author:** {{ tool_data.author }}

    **Dock Width:**{ title="Standard: 60mm<br>Wide: 76mm" } {{ tool_data.dock_width.capitalize() }}

    **Short Dock:**{ title="The height of the dock (Z axis) being less than standard. For Voron printers, the shorter height is not available for larger toolheads. Compatibility with Door Buffer varies depending on toolhead configuration. For Micron printers the short variant is a requirement." } {{ ':fontawesome-solid-check:{ style="color:green;" }' if tool_data.short_dock else ':fontawesome-solid-xmark:{ style="color:red;" }' }}

    **Stubby Dock:**{ title="The depth of the dock (Y axis) being less than standard and is not compatible with Door Buffer and is only available for the smaller toolheads." } {{ ':fontawesome-solid-check:{ style="color:green;" }' if tool_data.stubby_dock else ':fontawesome-solid-xmark:{ style="color:red;" }' }}

    | Size | Max Tools |
    |--------------|------------|
    | 250mm Voron  | {{ v250 }} |
    | 300mm Voron  | {{ v300 }} |
    | 350mm Voron  | {{ v350 }} |
    | 180mm Micron | {{ m180 }} |

    [:fontawesome-brands-github: View on GitHub]({{ tool_data.url }}){:target="_blank" .md-button}

{% endfor %}

</div>

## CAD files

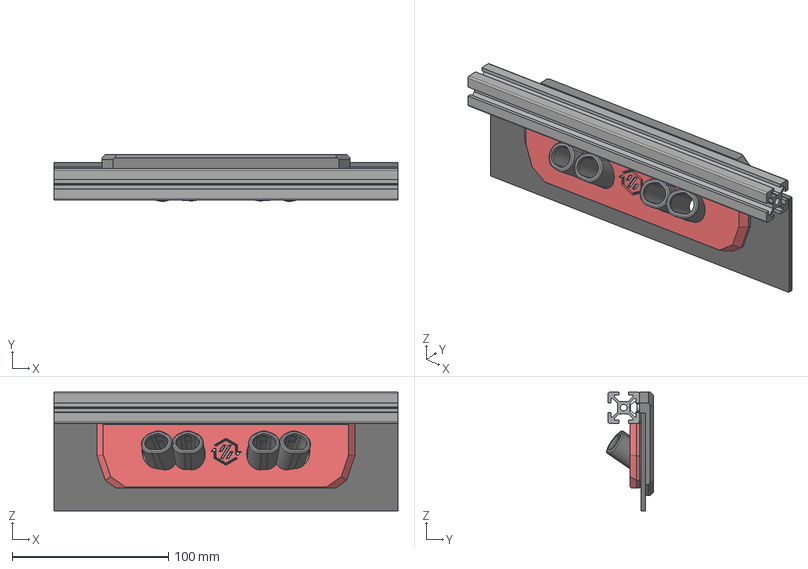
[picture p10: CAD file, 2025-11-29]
step_files/Cable Mangement/Umbilical Plate.step
220.0 x 29.9 x 76.1 mm
Frame
Foam Tape (1mm) (1) (3)
Face Plate_part
Logo Insert_part
Hexes_part
Outer_part
1mm Foam
M3 Threaded Insert (3) (8) (1) x 4
M3x10 SHCS (7) x 4
2020 Drop-in T-nut, M5 (8)
2020 Drop-in T-nut, M5 (7)
M5x10 BHCS (1) x 2

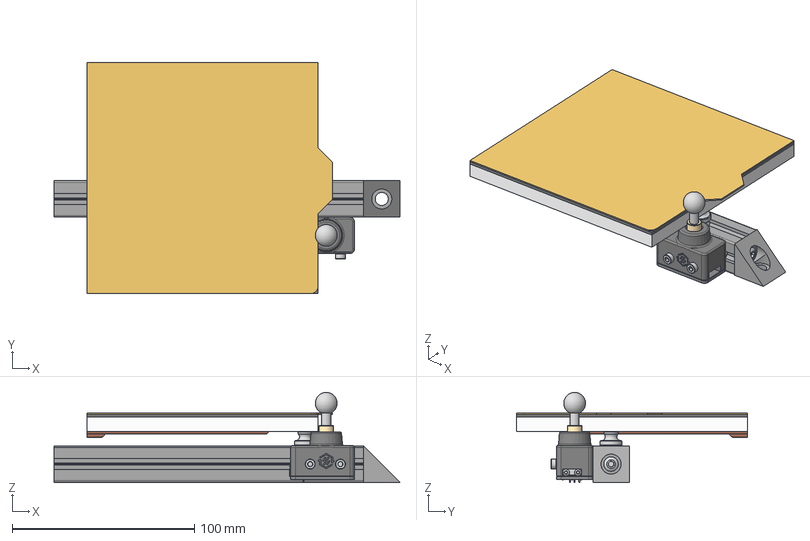
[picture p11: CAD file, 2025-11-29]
step_files/Calibration/Sexball_Probe.step
190.0 x 127.0 x 49.6 mm
Endstop Block
Omron_D2F_F
JST - XH - Thru (R) - 3Pin - 2.54mm
M2x10 STS_1
M2x10 STS_2
M3x20 SHCS
M3x20 SHCS_1
hammerhead nut v1
hammerhead nut v1 (1)
Shaft
Ball
8x10x5mm Bushing
10in MIC6 Plate
Magnet Sheet
Flex Sheet
Bed heater
M4 Knurled Nut DIN 466-B
M3x16 SHCS (2)
M5x16 BHCS (21)
2020 Drop-in T-nut, M3
HFSB5-2020-370-TPW (9)
90deg Corner (OpenBuilds)

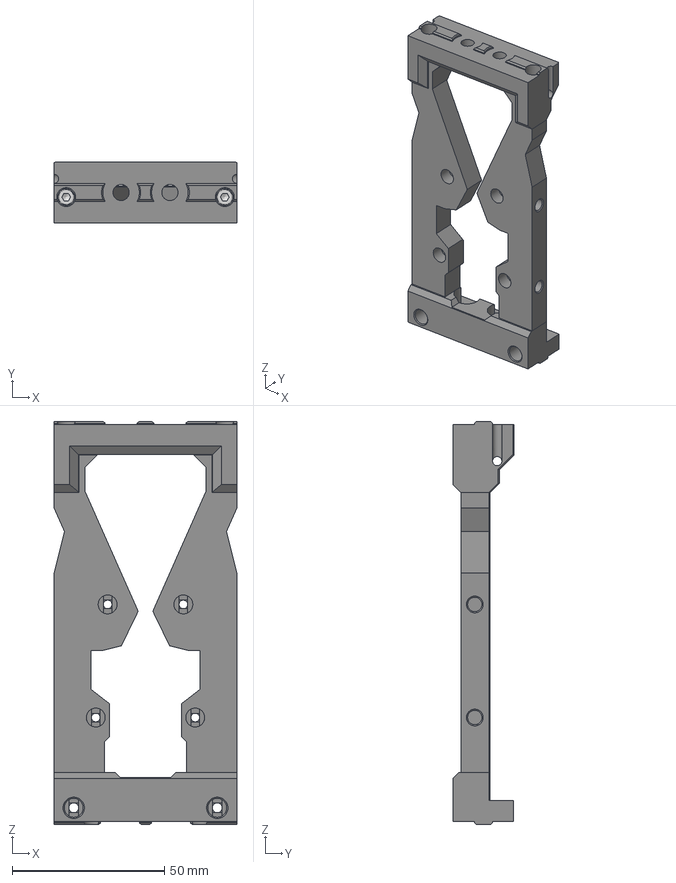
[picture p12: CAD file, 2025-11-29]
step_files/Docks/Frame - 2020 Short.step
60.0 x 20.0 x 132.2 mm
M3 Threaded Insert (3)_1_2 x 4
M3x16 SHCS x 4
Bottom
Top
Left (1)
Right (1)
M3 Threaded Insert (3)_1_1 x 2

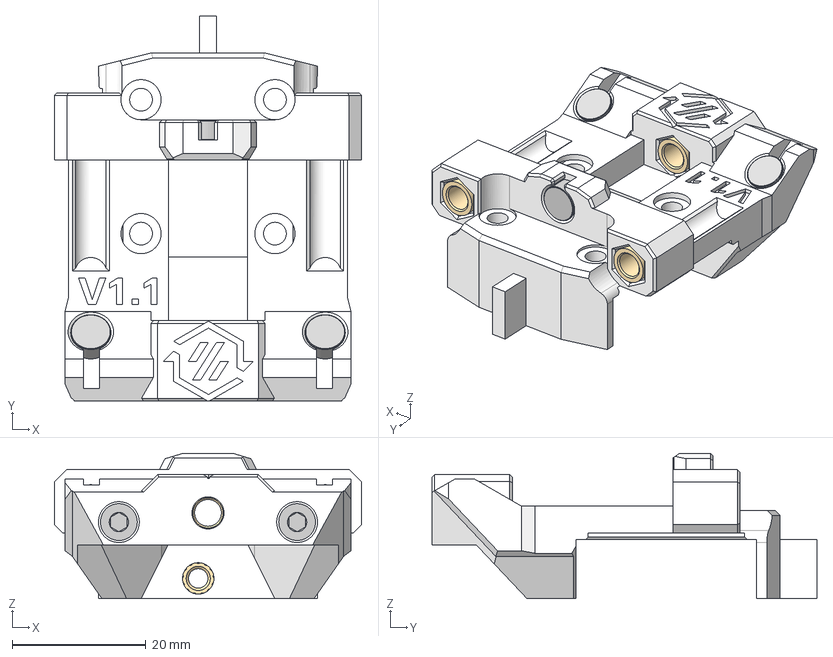
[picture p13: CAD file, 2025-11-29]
step_files/Shuttles/Shuttle_MGN12.step
45.9 x 57.5 x 21.7 mm
Shuttle MGN12
Bushings x3
6x3mm Magnets x3
(Unsaved)
M3x40 SHCS

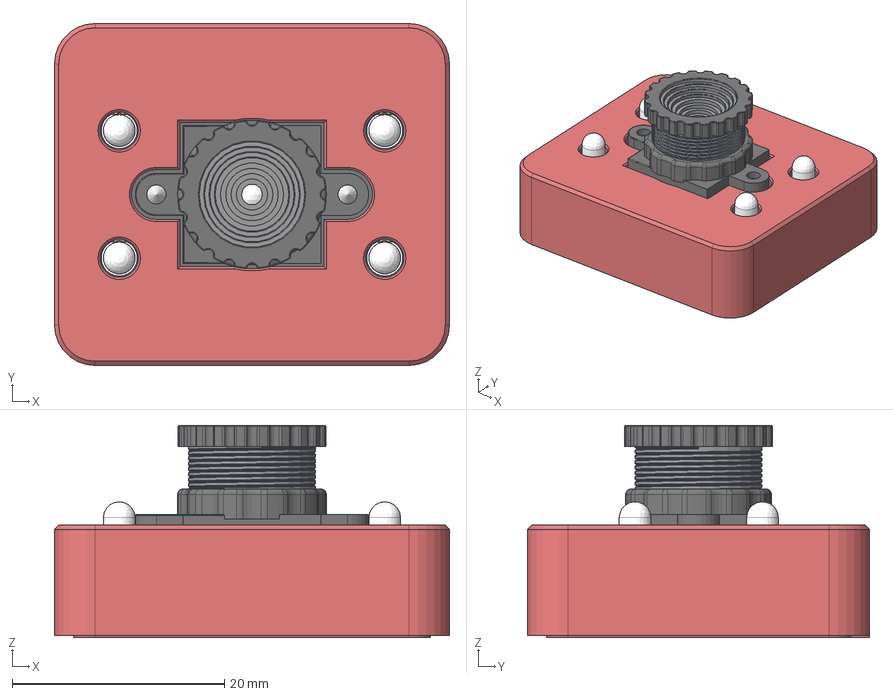
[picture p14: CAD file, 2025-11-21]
step_files/Usermods/Axiscope_Camera.step
37.2 x 32.2 x 20.0 mm
Copy of SOT 23^OV9726 Camera module x 3
Copy of 0402c_2320560^OV9726 Camera module x 28
cross fh tapping 7976_din_Tapping screw DIN 7982-ST2.2x4.5-C-H-N x 2
Copy of TSOP-6^OV9726 Camera module
Copy of QFN36 6x6^OV9726 Camera module
Copy of sm04b-srss-tb_lf__sn_^OV9726 Camera module
Copy of tsop8^OV9726 Camera module
Case Upper
Case Lower
6x3 Magnet x 4
LED x 4
Diode Silkscreen
LED Bulbs

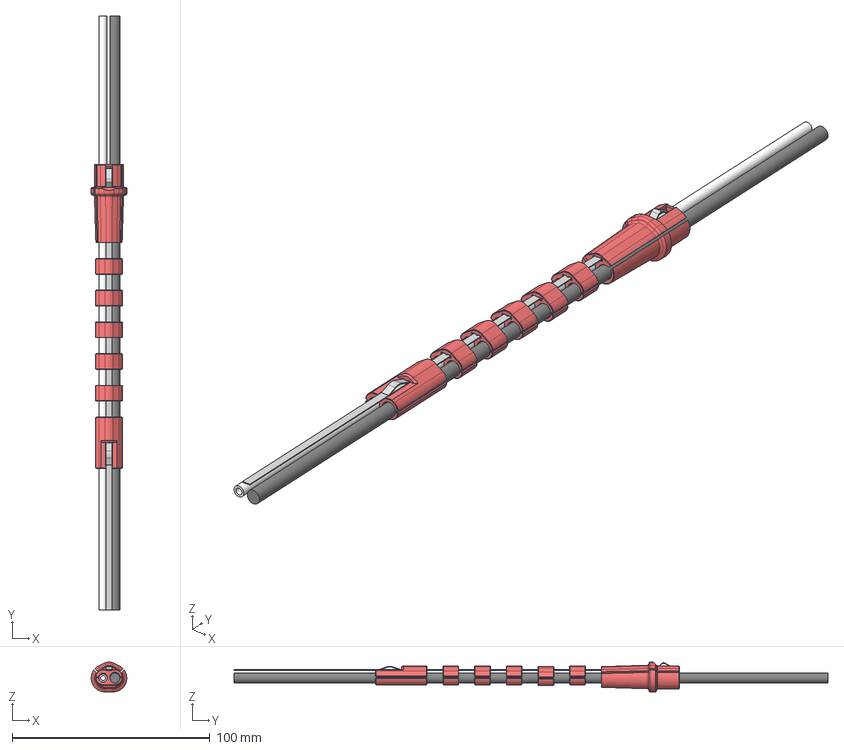
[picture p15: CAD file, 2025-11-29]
step_files/Cable Mangement/Umbilical.step
18.0 x 300.0 x 15.1 mm
[tpu]_Relief_Voron_x5xN_part
[tpu]_Terminator_Voron_xN_part
[tpu]_Clip_Voron_xN_part
Spring Steel Bend
[tpu]_Clip_Voron_xN_part_1
Wire
PTFE
[tpu]_Clip_Voron_xN_part_2
[tpu]_Clip_Voron_xN_part_3
[tpu]_Clip_Voron_xN_part_4
Spring Steel

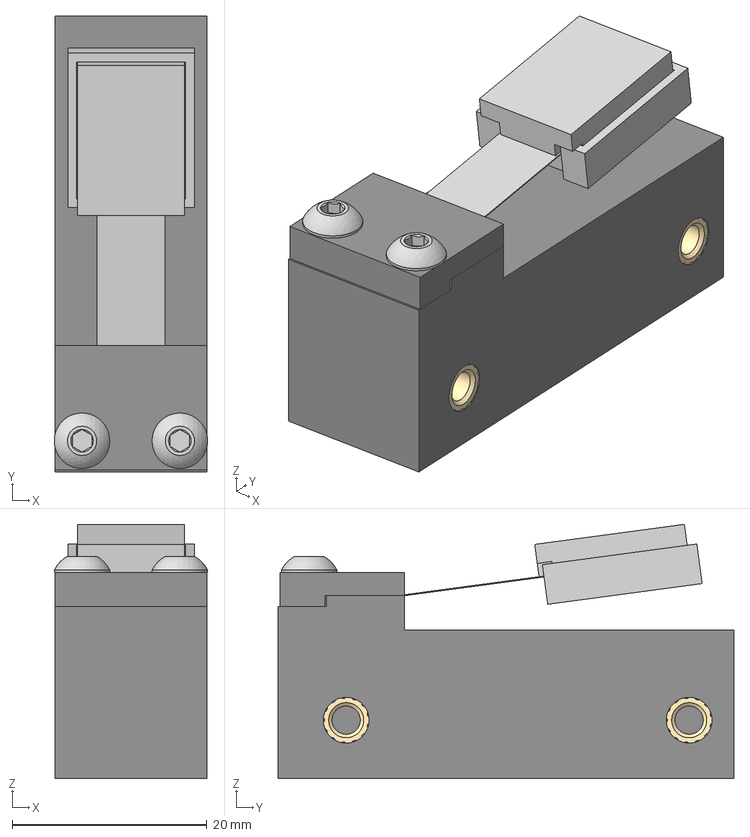
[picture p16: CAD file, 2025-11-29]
step_files/Docks/Blocker - Spring Steel.step
15.7 x 46.8 x 26.1 mm
Clamp
Silicone Jig
(Unsaved) x 6
M3x8 BHCS x 2
Spring Steel Body
Spring Steel Blocker
Silicone

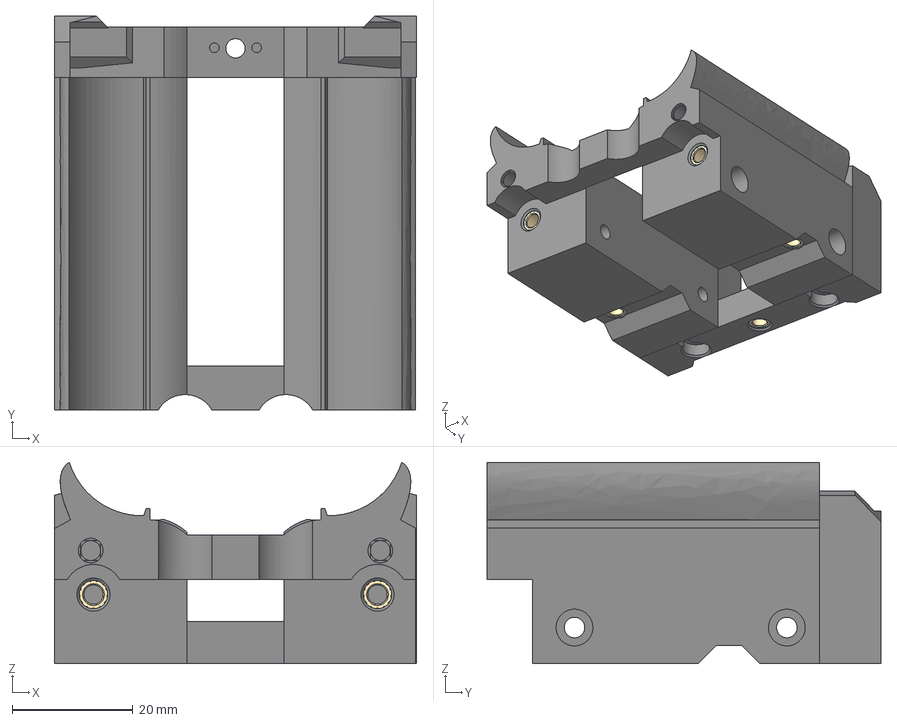
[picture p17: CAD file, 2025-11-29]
step_files/Docks/Base - DragonBurner.step
60.0 x 65.3 x 33.4 mm
M3 Threaded Insert (3) (8) (1) x 6
Base (1)
Back (5)
M3 Threaded Insert (3) (8) (1)_1

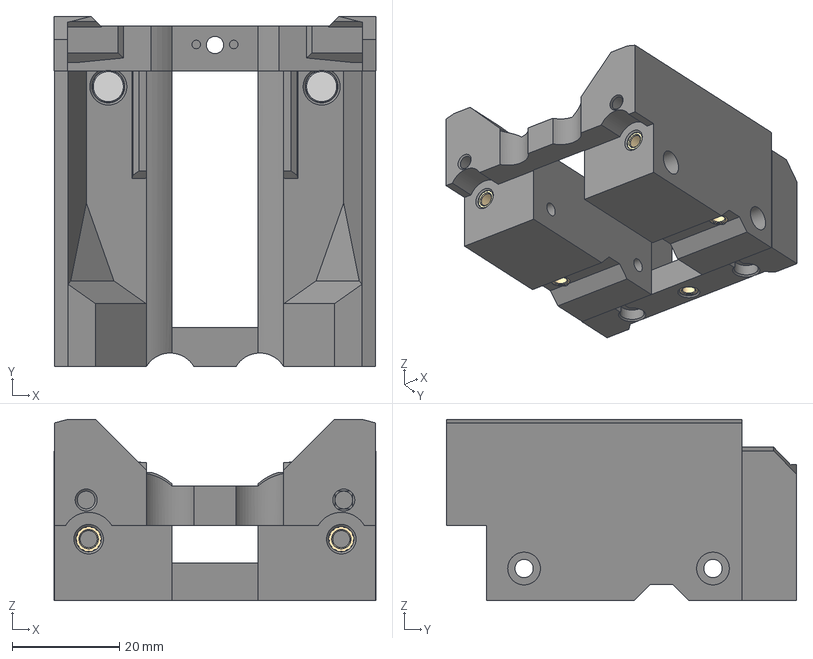
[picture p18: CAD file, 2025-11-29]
step_files/Docks/Base - Anthead.step
60.0 x 65.3 x 33.8 mm
Back (1)
Base (7)
M3 Threaded Insert (3) (8) (1) x 6
6x3mm Magnet (1)
6x3mm Magnet
M3 Threaded Insert (3) (8) (1)_1

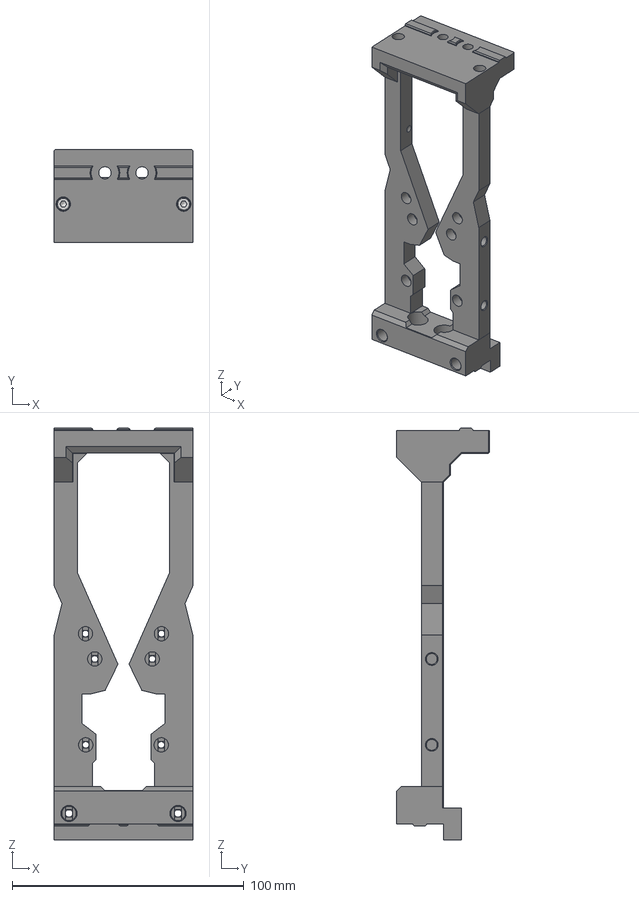
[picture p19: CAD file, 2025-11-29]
step_files/Docks/Frame - Crossbar.step
60.0 x 40.0 x 177.9 mm
M3x16 SHCS x 4
M3 Threaded Insert (3)_1_1 x 6
Left
Right
Bottom Crossbar
Top Crossbar

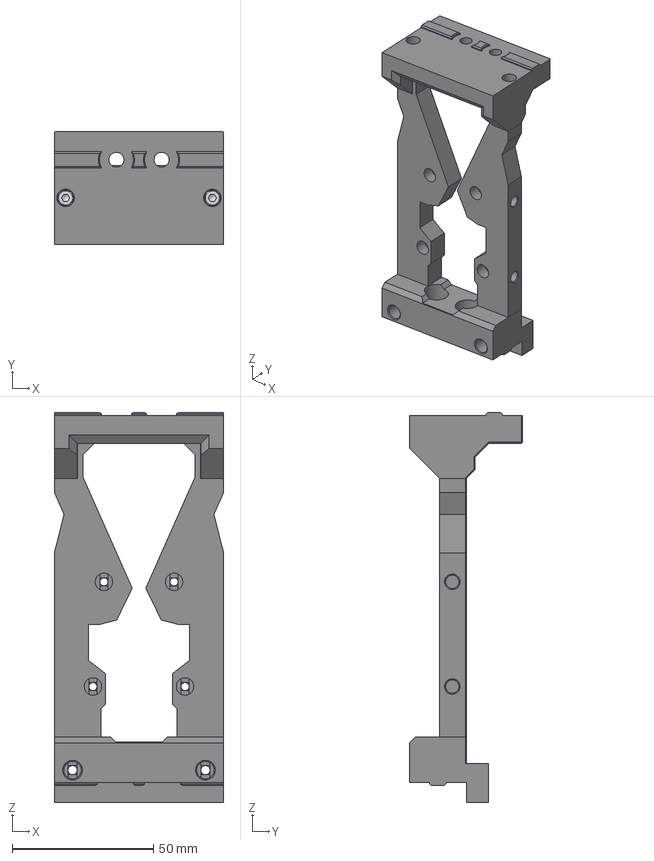
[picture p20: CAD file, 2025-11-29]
step_files/Docks/Frame - Crossbar Short.step
60.0 x 40.0 x 138.2 mm
M3x16 SHCS x 4
M3 Threaded Insert (3)_1_1 x 2
Left (1)
Right (1)
Bottom Crossbar
Top Crossbar
M3 Threaded Insert (3)_1_2 x 4

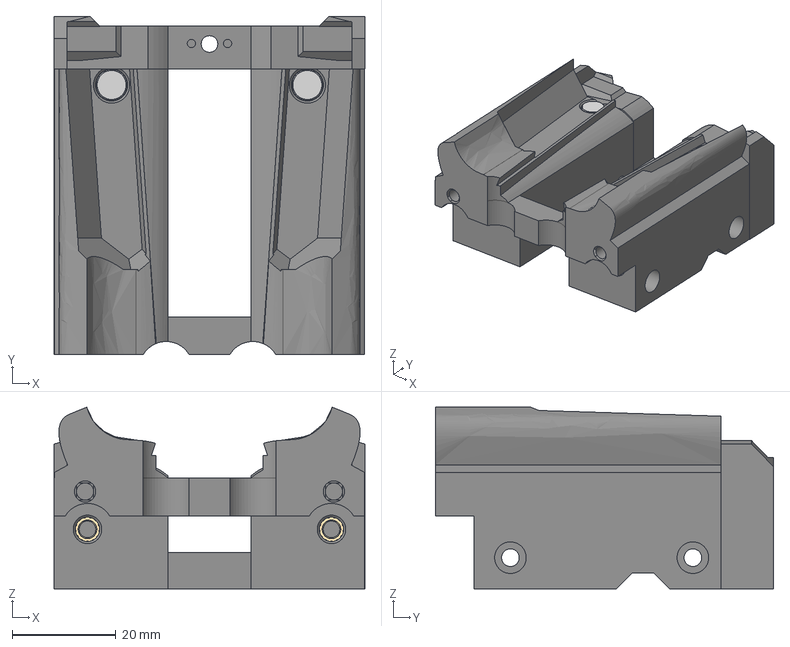
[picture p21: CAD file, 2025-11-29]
step_files/Docks/Base - Yavoth.step
60.0 x 65.3 x 35.0 mm
M3 Threaded Insert (3) (8) (1) x 6
6x3mm Magnet (1) (1)
6x3mm Magnet (2)
M3 Threaded Insert (3) (8) (1)_1
Base (1) (1)
Back (5) (1)

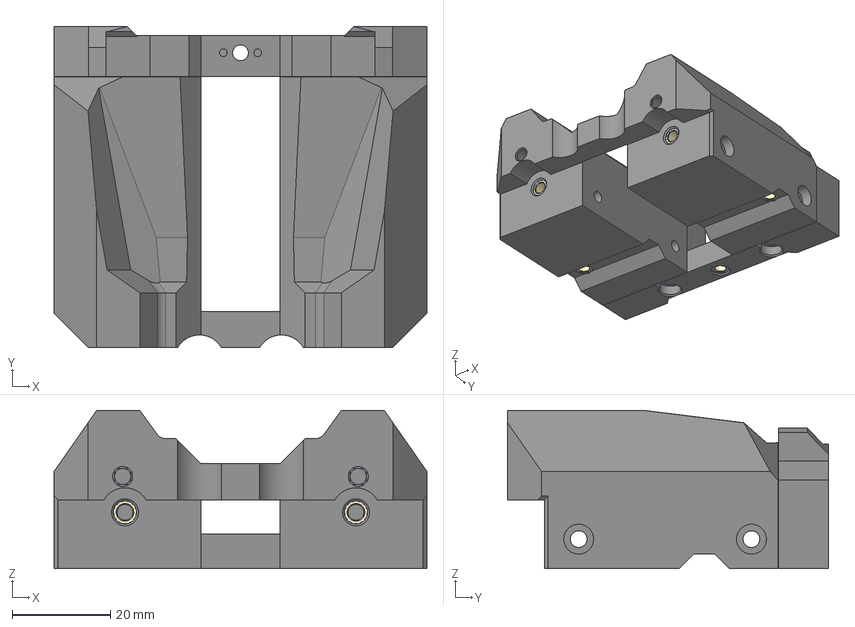
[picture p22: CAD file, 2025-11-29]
step_files/Docks/Base - A4T.step
76.0 x 65.4 x 32.2 mm
Base (2) (1) (1)
Back (3) (1) (1)
M3 Threaded Insert (3) (8) (1) x 4
M3 Threaded Insert (3) (8) (1)_1 x 2
M3 Threaded Insert (3) (8) (1)_1_1

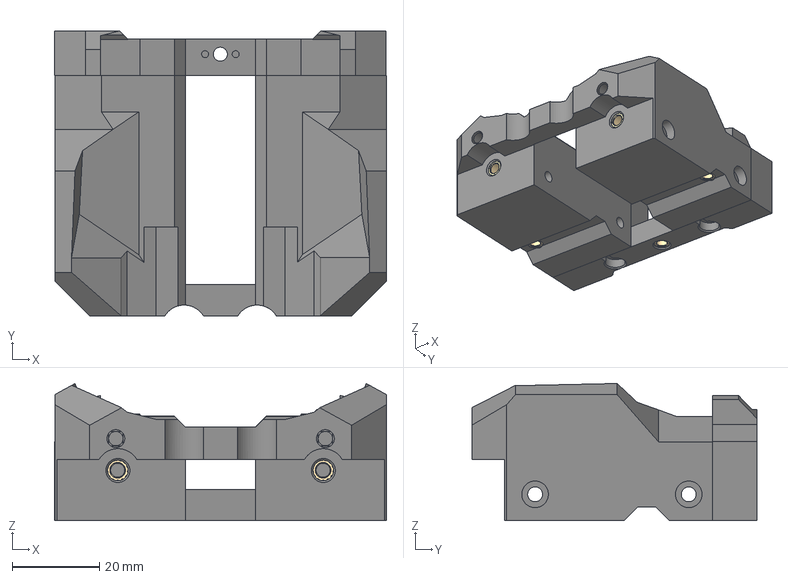
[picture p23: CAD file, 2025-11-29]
step_files/Docks/Base - StealthBurner.step
76.1 x 65.4 x 31.4 mm
M3 Threaded Insert (3) (8) (1) x 4
M3 Threaded Insert (3) (8) (1)_1 x 2
M3 Threaded Insert (3) (8) (1)_1_1
Back
Base

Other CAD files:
step_files/Docks/Base - JabberWocky.step
step_files/Docks/Base - BlackBird.step
step_files/Docks/Base - Mini StealthBurner.step
step_files/Docks/Blocker - Cup.step
step_files/Docks/Base - XOL.step
step_files/Docks/Frame - 2020.step

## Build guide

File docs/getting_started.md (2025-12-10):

# Getting Started

Before diving into your own StealthChanger build, please read the sections below — each covers essential information to ensure a successful and safe build. 

## Printing
All parts for StealthChanger should be printed using the Voron printing recommendation, except the 3d printed shuttle which also requires supports.

* `Layer Height` - 0.2mm
* `Extrusion Width` - 0.4mm, forced
* `Infill Percentage` - 40%
* `Infill Type` - Grid, Gyroid, honeycomb, Triangle or Cubic
* `Wall Count` - 4
* `Solid Top/Bottom Layers` - 5
* `Layer Height` - 0.2mm
* `Supports` - As required

## Print Tuning
Your printer needs to print dimensionally accurate parts due to the tolerances required when meshing multiple pins and bushings together.
It is highly recommended that before printing the shuttle and tool back plates for StealthChanger, your printer and filament be tuned for dimensional accuracy. 

!!! info "But but but, my prints look great!"
    Dimensional accuracy is often overlooked when our printers are making amazing looking parts. If you experience any binding or resistance while meshing the StealthChanger backplate to the shuttle, most often it is dimensional accuracy that is likely the culprit. This becomes even more evident when combining CNC shuttle with a printed tool back plate. 
    
    Many have found great success using [Califlower](https://vector3d.shop/products/califlower-calibration-tool-mk2){:target="_blank"} or one of its [derivatives](https://www.printables.com/search/models?q=califlower){:target="_blank"} to achieve the required dimensional accuracy for these high tolerance pieces.

## Losses
The addition of more tools and docks inside the printer typically means you end up with some lost printable build-volume. There should not be much loss in XY bed space, but whenever printing underneath the dock there is limited Z travel. These losses vary based on the printer’s configuration, as well as the selected tool and dock.

!!! info "So I can just increase the size of my Z axis to get rid of losses?"
    Increasing the height of the printer is often the first thing that comes to mind when trying to maintain the full printable area, unfortunately it also requires increasing the length of the umbilical for each tool which can become troublesome.

    If you require 100% of your build area, consider instead extending the printer in the Y axis. This will move the docks outside of the printable area of the bed and keep the umbilical at a shorter length as they only need to reach past the bed while at the top of the machine where there is more slack. These extended-Y Vorons have been dubbed [Vorlong](https://github.com/DraftShift/StealthChanger/tree/main/UserMods/TheSin-/Vorlong_%2B100y){:target="_blank"}.

## Community
StealthChanger has an active and helpful community on both [Discord](https://discord.gg/draftshift) and [facebook](https://www.facebook.com/groups/449879874593718/), if you get stuck at any point, don't hesitate to reach out and ask for help.

!!! info "User Mods"
    There are many [usermods](https://github.com/DraftShift/StealthChanger/tree/main/UserMods){target="_blank"} that can modify or enhance the many aspects the StealthChanger ecosystem. If you can't find what your after in the main repository, it's likely that one of our talented community members has created a user mod for it.

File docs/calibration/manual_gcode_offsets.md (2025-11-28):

{% macro code_block(lines="8 9 10") %}
``` cfg title="[tool Tn] example." hl_lines="{{ lines }}"
  [tool T1]
  tool_number: 1 # change to the index of the tool. 0, 1, 2, etc.
  extruder: extruder1 # change to match the extruder you are configuring: extruder, extruder1, etc.
  fan: T1_part_fan
  params_park_x: 0 # The absolute X-position of the tool in its dock.
  params_park_y: 0 # The absolute Y-position of the tool in its dock.
  params_park_z: 0 # The absolute Z-position where the tool and shuttle mate in the dock, determined when the TAP (or Z-probe) triggers.
  gcode_x_offset: 0 # The X-Axis offset of the nozzle's orifice in relation to tool 0
  gcode_y_offset: 0 # The Y-Axis offset of the nozzle's orifice in relation to tool 0
  gcode_z_offset: 0 # The Z-Axis offset of the nozzle's orifice in relation to tool 0
```
{% endmacro %}

Manual calibration uses a paper test to measure Z-offsets between tools.

!!! note "Critical"
    - Only home or probe with T0 during this calibration

### G-code Z Offset

{{ code_block(lines="10") }}

1. Ensure **T0 is on the shuttle**
2. Run: `INITIALIZE_TOOLCHANGER`
3. Home the printer: `G28`.
4. Level the gantry: `QUAD_GANTRY_LEVEL`.
5. Home Z again: `G28 Z`.
6. Raise the nozzle 10mm: `G1 Z10 F600`.

7. Manually remove the current tool and place the next tool on the shuttle
8. Perform a [manual paper test](#manual-paper-test) and adjust Z until you feel slight resistance
9. Once satisfied, run `M114` and copy the Z value from the console.
10. Update the `gcode_z_offset` value in `[tool Tn]` section of the tool's config file
11. Repeat from **step 6** for all remaining tools
12. Run: `FIRMWARE_RESTART`

### Manual Paper Test

The “paper test” involves placing a standard sheet of paper between the build plate and the nozzle, then carefully jogging the nozzle downward until you feel slight resistance as the paper is moved back and forth.

!!! tip "Key Points"
    - Use regular copy paper (approximately 100 microns / 0.1mm thick)
    - Always perform the test at **room temperature** (both nozzle and bed cold)
    - Ensure the nozzle and bed are clean and free of debris
    - Use the same surface/tape that you normally print on

1. Cut a small piece of paper (approximately 5x3 cm).
2. Place it between the nozzle and bed.
3. Using manual movements (Mainsail/Fluidd/KlipperScreen), jog the nozzle down in small increments.
4. Push the paper back and forth to feel for resistance.
5. Continue until you feel slight friction (paper can slide but with resistance)

### G-code XY Offsets

{{ code_block(lines="8 9") }}

Calibrating XY offsets manually, involves doing test prints, visually examining the alignment and adjusting between tests. This procedure gets repeated until you are happy with the alignment.

- For manual XY calibration we recommend first using the [IDEX calibration tool](https://www.printables.com/model/201707-x-y-and-z-calibration-tool-for-idex-dual-extruder){target="_blank"} to get each tool's nozzle aligned to T0. 
- Follow that up with the [StealthChanger Logo Test Chip](https://www.printables.com/model/1092898-stealthchanger-logo-test-chip){target="_blank"} to ensure all offsets are working harmoniously.

<iframe src="https://www.printables.com/embed/201707" width="300" height="340" scrolling="no" frameborder="0"></iframe>
<iframe src="https://www.printables.com/embed/1092898" width="300" height="340" scrolling="no" frameborder="0"></iframe>

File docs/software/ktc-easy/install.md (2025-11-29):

## Clone and Install
Connect to the printer via SSH and enter the following commands:

``` bash { .copy }
cd ~/
git clone https://github.com/jwellman80/klipper-toolchanger-easy.git
cd ~/klipper-toolchanger-easy
./install.sh
```

You will be prompted to decide a Z probe solution. A typical StealthChanger uses the built-in tap sensor for probing and option 1 should be chosen.

``` bash
1. I will use the TAP sensor as my Z probe on each tool
2. I will use a shuttle mounted Beacon/Cartographer/Eddy/etc as my Z probe
```

!!! example "Eddy Current"
    Eddy current sensors on StealthChanger have additional requirements and some limitations, they are considered experimental. 

## File Structure
After installation, your configuration will be organized as follows:

```
~/printer_data/config/toolchanger/
├── readonly-configs/           # DO NOT EDIT - Symlinked macros
│   ├── homing.cfg
│   ├── tool_detection.cfg      # TAP install only
│   ├── toolchanger.cfg
│   ├── toolchanger-macros.cfg
│   ├── calibrate-offsets.cfg
│   ├── crash-detection.cfg
│   └── toolchanger-include.cfg
├── tools/                      # Tool-specific configurations
│   ├── example_T0.cfg          # Example configurations
│   └── example_T1.cfg
└── toolchanger-config.cfg      # User-editable overrides
```

## Include Configs
Include the configuration by adding the following to the start of your `printer.cfg`
``` cfg { .copy }
[include toolchanger/readonly-configs/toolchanger-include.cfg]
```

## Moonraker Config
Optional, but recommended, add the following to your `moonraker.conf` to enable automatic updates:

``` cfg { .copy }
[update_manager klipper-toolchanger-easy]
type: git_repo
path: ~/klipper-toolchanger-easy
origin: https://github.com/jwellman80/klipper-toolchanger-easy.git
managed_services: klipper
primary_branch: main
```

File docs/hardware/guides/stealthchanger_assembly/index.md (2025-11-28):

# Stealthchanger Assembly

{% set guides = get_hardware("stealthchanger_assembly") %}
{% include "_templates/guide_cards.md" %}

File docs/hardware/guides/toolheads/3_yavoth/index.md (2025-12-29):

# Yavoth

{% set assembly = get_hardware("toolheads")["Yavoth"] %}

{% include "_templates/overview.md" %}

## Assembly
{% include "_templates/assembly_viewer.md" %}

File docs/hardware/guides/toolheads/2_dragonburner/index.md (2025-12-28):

# DragonBurner

{% set assembly = get_hardware("toolheads")["DragonBurner"] %}

{% include "_templates/overview.md" %}

## Assembly
{% include "_templates/assembly_viewer.md" %}

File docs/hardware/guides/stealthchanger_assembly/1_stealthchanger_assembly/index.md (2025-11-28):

# Stealthchanger Assembly

{% set assembly = get_hardware("stealthchanger_assembly")["Stealthchanger Assembly"] %}

{% include "_templates/overview.md" %}

## Assembly
{% include "_templates/assembly_viewer.md" %}

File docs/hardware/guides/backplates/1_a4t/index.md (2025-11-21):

# A4T Backplate

{% set assembly = get_hardware("backplates")["Backplate - A4T"] %}

{% include "_templates/overview.md" %}

## Assembly
{% include "_templates/assembly_viewer.md" %}

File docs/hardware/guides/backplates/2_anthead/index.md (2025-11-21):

# Anthead Backplate

{% set assembly = get_hardware("backplates")["Backplate - Anthead"] %}

{% include "_templates/overview.md" %}

## Assembly
{% include "_templates/assembly_viewer.md" %}

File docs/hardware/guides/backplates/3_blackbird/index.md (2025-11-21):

# BlackBird Backplate

{% set assembly = get_hardware("backplates")["Backplate - BlackBird"] %}

{% include "_templates/overview.md" %}

## Assembly
{% include "_templates/assembly_viewer.md" %}

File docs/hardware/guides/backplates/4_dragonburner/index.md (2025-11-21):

# DragonBurner Backplate

{% set assembly = get_hardware("backplates")["Backplate - DragonBurner"] %}

{% include "_templates/overview.md" %}

## Assembly
{% include "_templates/assembly_viewer.md" %}

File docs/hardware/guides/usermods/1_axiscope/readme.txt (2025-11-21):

This is an example of how you can create usermod guides. See CONTRIBUTING_GUIDES.md for more information.

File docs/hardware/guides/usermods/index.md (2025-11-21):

# Usermods
A collection of user provided additions and modifications. If you would like your usermod to be featured, consider reading [Contributing Guide](https://github.com/DraftShift/Docs/blob/main/CONTRIBUTING_GUIDES.md){target="_blank"} and submitting a [pull request](https://docs.github.com/en/pull-requests/collaborating-with-pull-requests/proposing-changes-to-your-work-with-pull-requests/creating-a-pull-request){target="_blank"}.
{% set guides = get_hardware("usermods") %}
{% include "_templates/guide_cards.md" %}

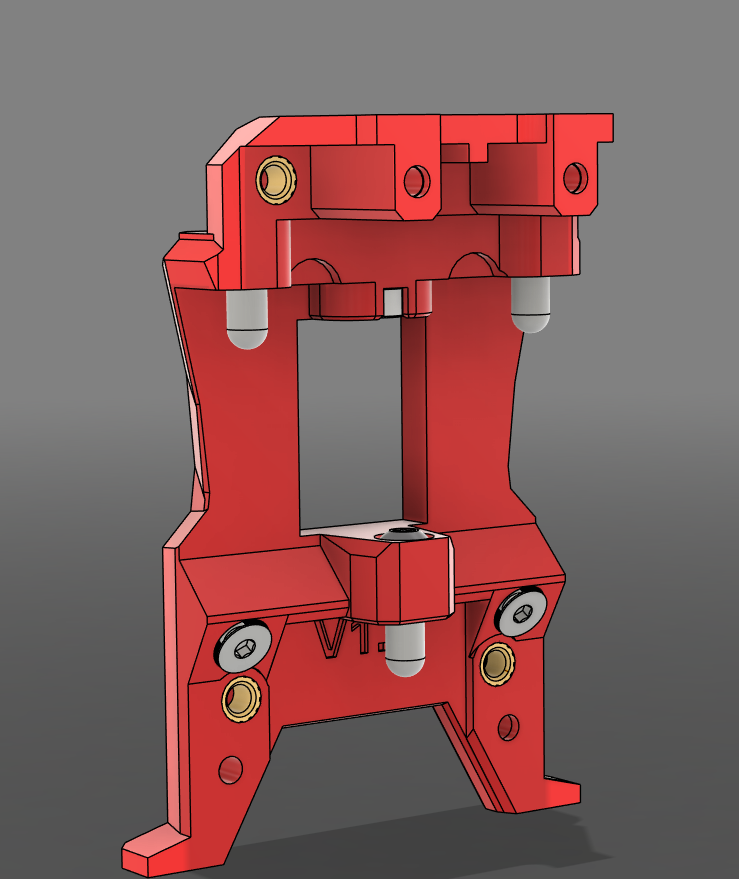
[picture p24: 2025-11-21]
docs/hardware/guides/backplates/7_stealthburner/image.png

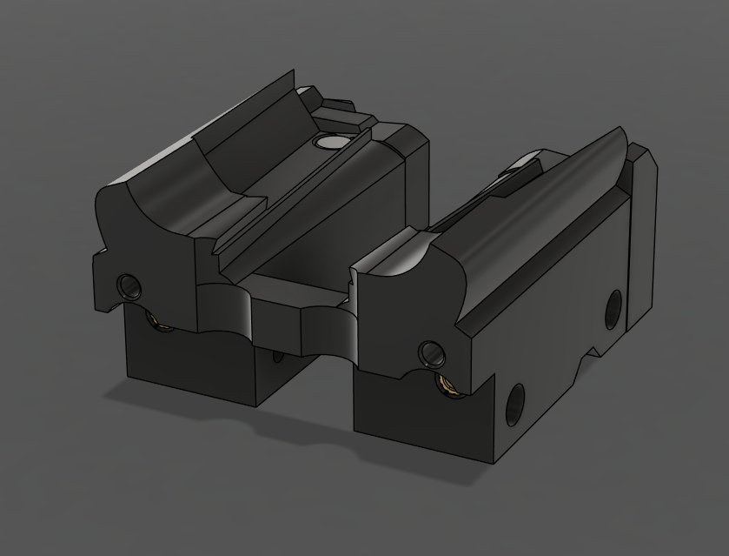
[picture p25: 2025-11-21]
docs/hardware/guides/modular_docks/11_base_yavoth/image.png

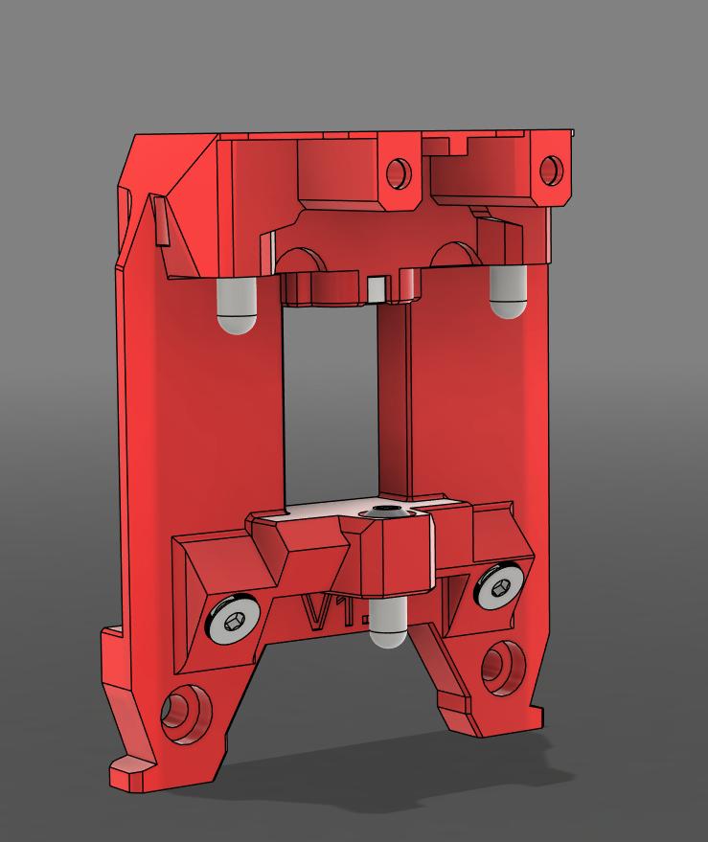
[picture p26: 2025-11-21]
docs/hardware/guides/backplates/2_anthead/image.png

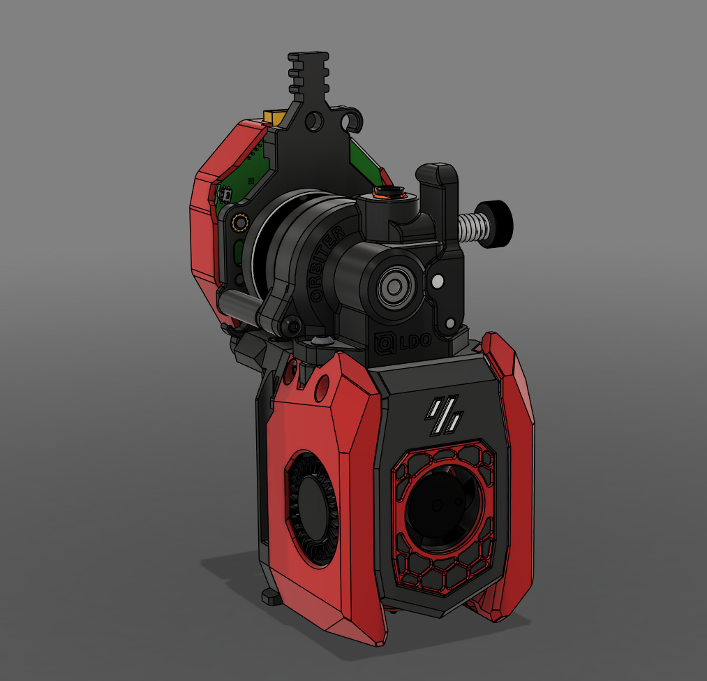
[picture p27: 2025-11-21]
docs/hardware/guides/toolheads/1_anthead/image.png

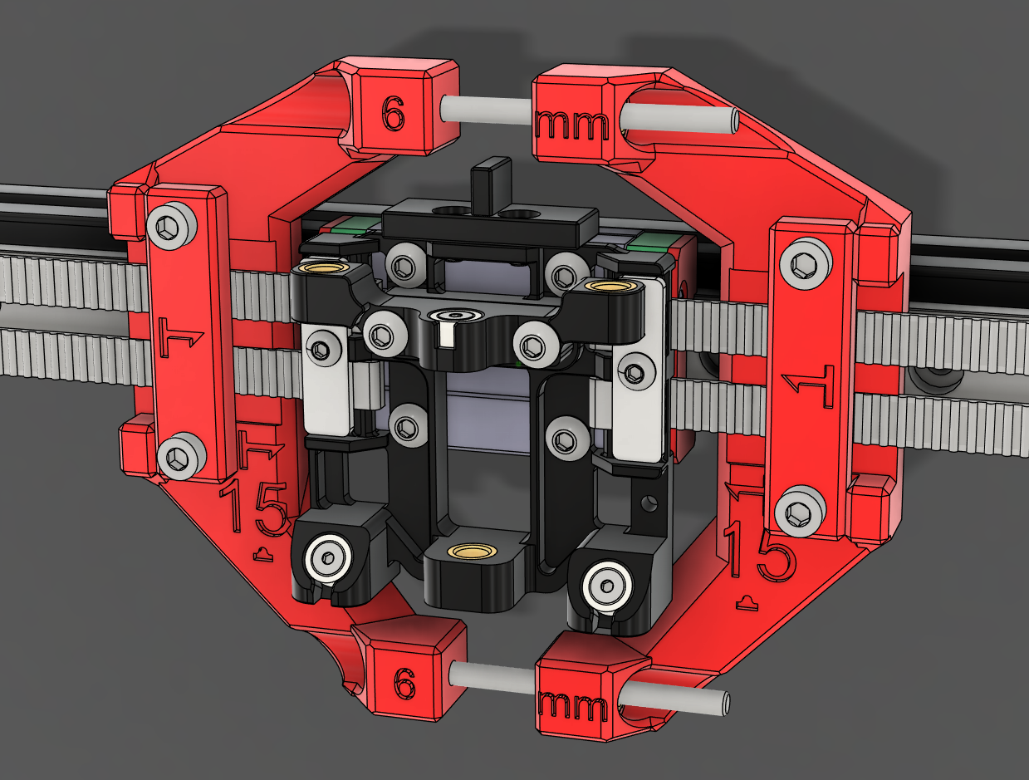
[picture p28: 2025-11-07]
docs/hardware/guides/shuttles/4_install_ldo/image.png

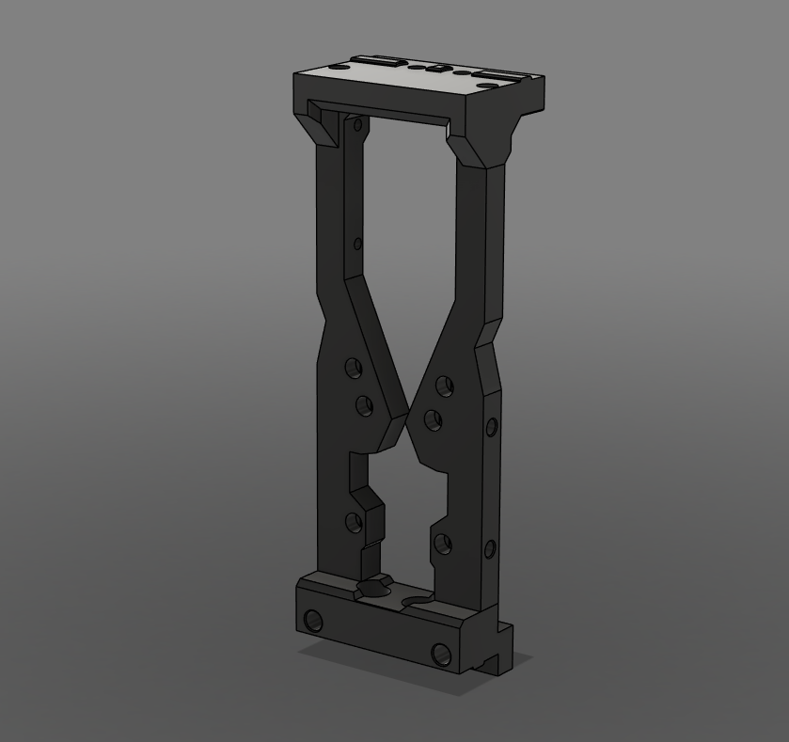
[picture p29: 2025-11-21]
docs/hardware/guides/modular_docks/15_frame_standard_crossbar/image.png

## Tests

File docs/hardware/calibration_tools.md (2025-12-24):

---
search:
  boost: 2 
---

Having multiple toolheads print on the same part introduces a new calibration challenge, as each toolhead must print precisely in relation to all the others. Therefore, each toolhead has to be calibrated in X, Y and Z to match the others.

## Sexball Probe
The Sexball gets its rather raunchy name from being a derivative of hartk's [Sexbolt Z Endstop](https://github.com/VoronDesign/VoronUsers/tree/main/printer_mods/hartk1213/Voron2.4_SexBolt_ZEndstop){:target="_blank"}. The addition of a ball at the end of the shaft allows it to do multi axis (XYZ) probing.

Converting an existing [Sexbolt Z Endstop](https://github.com/VoronDesign/VoronUsers/tree/main/printer_mods/hartk1213/Voron2.4_SexBolt_ZEndstop){:target="_blank"} is easy, all you need is to replace the existing shaft with a M5 threaded (one end) shaft and 12mm threaded ball.

!!! warning "Not just any Z endstop"
    Only Z endstops with a bushing are recommended for use as a Sexball Probe. If your Z endstop is the style with a deflanged pulley, you will need to source another one.

Sexball Probe

!!! tip "LDO Kit"
    All of the hardware components for a Sexball Probe come as a part of LDO's `Base StealthChanger Kit`.

## Community Tools

### Axiscope

[Axiscope](https://github.com/nic335/Axiscope){target="_blank"} is a specialized tool created by members of our community that is designed to simplify the calibration process for multi-tool 3D printers running [Klipper-toolchanger](../software/index.md#klipper-toolchanger){:target="_blank"} using camera-assisted alignment.

[Axiscope](https://github.com/nic335/Axiscope){target="_blank"} provides a streamlined web interface for:

* Semi-automated XY calibration using camera feedback.
* Automated Z alignment through use of a Z endstop or [Sexball Probe](#sexball-probe).
* Quick and precise tool alignment.
* No calculations required, the offsets are given to you in the exact format used with [Klipper-toolchanger](../software/index.md#klipper-toolchanger).

Axiscope

!!! tip "Which Camera?"
    [Axiscope](https://github.com/nic335/Axiscope){target="_blank"} can technically use any webcam, but it's recommended to use a camera that is built for purpose. See our [build guide](guides/usermods/N3MI%20-%20axiscope/index.md) on how to assemble a camera specifically for Axiscope or consider [Ember Prototype's CXC camera](https://www.emberprototypes.com/products/cxc){:target="_blank"}.

More information can be found on the [Axiscope Github](https://github.com/nic335/Axiscope){:target="_blank"}.

### Nudge

Nudge is a multi axis probe where the shaft is suspended in a wobbler using magnets and screws. Nudging the probe in any axis breaks contact with screws within the probe which triggers the probe.

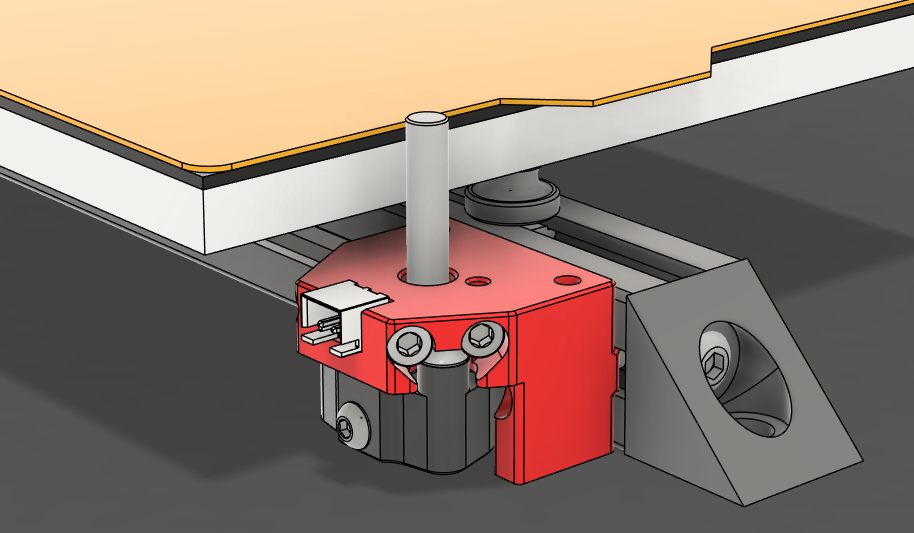
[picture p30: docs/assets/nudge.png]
Nudge


For more information and build instructions, visit the [Nudge GitHub](https://github.com/zruncho3d/nudge){:target="_blank"}.

## Calibration Prints

If you don't have any nozzle calibration aids at your disposal, test prints are a simple and reliable way to get your nozzles aligned. 

Test prints work by doing a print with 2+ tools and studying the alignment manually. Adjust the offset by the measured amount and print again. Repeat these steps until you are happy with alignment.

<iframe src="https://www.printables.com/embed/201707" width="300" height="340" scrolling="no" frameborder="0"></iframe>
<iframe src="https://www.printables.com/embed/1092898" width="300" height="340" scrolling="no" frameborder="0"></iframe>

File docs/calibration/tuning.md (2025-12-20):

## Resonance
Typically, each toolhead board will have its own accelerometer for resonance testing. 
Each accelerometer needs to be given a unique name in Klipper so that it can be called directly.

``` cfg title="Example of tool's Nitehawk36 ADXL345 configuration."
[adxl345 T0]
cs_pin: NHK0:gpio27
spi_software_sclk_pin: NHK0:gpio18
spi_software_mosi_pin: NHK0:gpio20
spi_software_miso_pin: NHK0:gpio19
axes_map: x,z,y
```

Klipper's [[resonance_tester]](https://www.klipper3d.org/Config_Reference.html#resonance_tester){target="_blank"} module only supports a single `accel_chip` to be set at a time. This means that any time you want to run input shaper, the accelerometer chip needs to be defined to ensure the correct toolhead board is being used. 

You can swap the accelerometer manually by changing the `accel_chip` in [[resonance_tester]](https://www.klipper3d.org/Config_Reference.html#resonance_tester){target="_blank"}.

``` cfg hl_lines="4" title="Example [input_shaper] & [resonance_tester] sections."
[input_shaper]

[resonance_tester]
accel_chip: adxl345 T0
probe_points: 175,175,20
sweeping_accel: 400
sweeping_period: 0
```

To run input shaper without changing the `accel_chip` in [[resonance_tester]](https://www.klipper3d.org/Config_Reference.html#resonance_tester){target="_blank"}, you can specify the accelerometer in the macro's parameters.

``` lua { .copy title="Shaketune input shaper example." }
AXES_SHAPER_CALIBRATION ACCEL_CHIP="'adxl345 T0'"
```

### Applying the Results
Each tool can have the frequency and shaper type defined for the X and Y axes in the [[tool Tn]](../software/ktc-easy/configuration/tool.md#tool) section by adding `params_input_shaper_freq_x`, `params_input_shaper_type_x`, `params_input_shaper_freq_y` and `params_input_shaper_type_y`.

``` cfg hl_lines="12 13 14 15" title="Example [tool Tn] section with input shaper"
[tool T0]
tool_number: 0
extruder: extruder
fan: T0_partfan
params_park_x: 5.0   # The absolute X-position of the tool in its dock.
params_park_y: 10.8  # The absolute Y-position of the tool in its dock.
params_park_z: 264.4 # The absolute Z-position where the tool and shuttle mate in the dock,determined when the TAP (or Z-probe) triggers.
gcode_x_offset: 0 # The X-Axis offset of the nozzle's orifice in relation to tool 0
gcode_y_offset: 0 # The Y-Axis offset of the nozzle's orifice in relation to tool 0
gcode_z_offset: 0 # The Z-Axis offset of the nozzle's orifice in relation to tool 0

params_input_shaper_freq_x: 62.2
params_input_shaper_type_x: 'ei'
params_input_shaper_freq_y: 41.0
params_input_shaper_type_y: 'mzv'

```

## Tool Change Speed
The speed of a tool change is determined by multiple factors.

1. The size of the printer.
2. The quality of components used.
3. The power given to the motors.
4. `max_velocity` in the `[printer]` section.
5. `max_accel` in the `[printer]` section.
6. `max_z_velocity` in the `[printer]` section.
7. `max_z_accel` in the `[printer]` section.
8. `params_fast_speed` in the `[toolchanger]` section.
9. `params_path_speed` in the `[toolchanger]` section.

The first 2 are choices made while building your printer, make sure to use quality motors and rails from reputable sources. The third depends on which PSU and motor drivers you have, and the rest are all settings that need to be tuned.

### Determining Power
Typically, a good starting point for the `run_current` of your motors is to use 40% of the motor's rated current. For example, if your motor is rated to 2a, `2*0.4=0.8`. Your starting `run_current` would be `0.8`. This can vary depending on the motor or manufacturer, but whether your running 24 or 48 volts, 40% of the motors rated current should yeild good results. 

Increasing the `run_current` could enable faster tool changes, but should be done with caution.

!!! danger "Hot Hot Hot"
    Voron 2.4 motor mounts are made from printed plastic. If they get too hot they will deform, causing catastrophic failure.

    When increasing the `run_current` of your motors, make sure to monitor the temperature of the motors during operation. If the temperature starts to get too hot, reduce the `run_current` and monitor the temperature again.

For more information on tuning your `run_current`, consult [Ellis' Print Tuning guide](https://ellis3dp.com/Print-Tuning-Guide/articles/determining_motor_currents.html){target="_blank"}.

### max_velocity and max_accel
`max_velocity` and `max_accel` are typically tuned as part of standard printer build and determine the maximum limit of how fast your printer can accelerate and move in the the XY axis.

For more information on `max_velocity` and `max_accel`, consult [Ellis' Print Tuning guide](https://ellis3dp.com/Print-Tuning-Guide/articles/determining_max_speeds_accels.html){target="_blank"}.

### max_z_velocity and max_z_accel
`max_z_velocity` and `max_z_accel` are typically overlooked on a standard printer build, but are rather important for StealthChanger. They determine the maximum limit of how fast your printer can accelerate and move in the the Z axis.

The standard Voron 2.4 example configurations are intentionally conservative regarding gantry Z movement speeds—and for good reason. If any one of the four Z-axis motors were to skip steps while the others continue to move, the gantry would become racked.

With StealthChanger, the gantry operates at significantly higher speeds than most stock configurations. If a Z-axis motor were to skip at these elevated speeds, the resulting misalignment of the gantry corners could be severe enough to cause significant damage to the gantry.

!!! warning "Flying too close to the sun"
    This is an example of what could happen if you tune you coinfiguration too high for the hardware you are using. Thanks to fireishott on Discord for the image.

    fireishot

#### Increasing Z speeds
Increasing the `max_z_velocity` and `max_z_accel` values should only be done once you are able to do tool changes and should be done in small increments.

``` cfg title="[printer] section example."
[printer]
kinematics: corexy
max_velocity: 300
max_accel: 3000
max_z_velocity: 100
max_z_accel: 1000 # Start with 500 for G2Z.
square_corner_velocity: 5.0
```

- Increase your `max_z_accel` in increments of 100-200 at a time. Test with multiple tool changes between increments.
- Increase your `max_z_velocity` in increments of 25-50 at a time. Test with multiple tool changes between increments.
- Reference [Prusa's Max Speed Calculator](https://blog.prusa3d.com/calculator_3416/#speed){target="_blank"} for a visual on how the values will be applied.

### params_fast_speed and params_path_speed
`params_fast_speed` and `params_path_speed` are klipper-toolchanger's way of limiting the speeds used for tool changes and are located in the [`[toolchanger]`](../software/ktc-easy/configuration/toolchanger.md#toolchanger) section of the [toolchanger-config](../software/ktc-easy/configuration/toolchanger.md). 

- `params_fast_speed` clamps the all movements to the dock at it's set value.
- `params_path_speed` clamps the all of the pickup or dropoff movements within the dock at it's set value.

``` cfg hl_lines="8 9" title="[printer] section example."
[toolchanger]
# These paths have been verified to work with StealthChanger with ModularDock, it should not be changed unless you understand what you are doing.
params_dropoff_path: [{'y':9.5 ,'z':4}, {'y':9.5, 'z':2}, {'y':5.5, 'z':0}, {'z':0, 'y':0, 'f':0.5}, {'z':-10, 'y':0}, {'z':-10, 'y':16}]
params_pickup_path: [{'z':-10, 'y':16}, {'z':-10, 'y':0}, {'z':0, 'y':0, 'f':0.5, 'verify':1}, {'y':5.5, 'z':0}, {'y':9.5, 'z':2}, {'y':9.5 ,'z':4}]

params_safe_y: 120 # The distance from absolute zero to the back of the tools in the dock. Allow some extra clearance.
params_close_y: 30 # The relative distance from safe_y the gantry moves to while changing tools.
params_fast_speed: 10000 # Movement speed while outside of the dock during tool changes.
params_path_speed: 900 # Movement speed used for pickup and dropoff during tool changes.
```

Increasing these values will result in faster tool change movement up to the point of reaching your `max_velocity`, `max_accel`, `max_z_velocity` and `max_z_accel` values. The `max_velocity`, `max_accel`, `max_z_velocity` and `max_z_accel` values will be used if `params_fast_speed` or `params_path_speed` exceeds them.

### Deminishing Returns
After tuning all of your currents and speeds, a typical Voron 2.4 should be capable of tool changes that are less than 10 seconds from the bed and back. 

With specialized hardware, faster speeds can be achieved, but you get to the point where there is little to no benifit. As per [Prusa's Max Speed Calculator](https://blog.prusa3d.com/calculator_3416/#speed), you can only accelerate so fast until reaching the maximum velocity. With the size of the standard Voron 2.4 being 350mm or less, you start to be limited by the time it takes to actually pickup the tool. 

You need to allow enough time for the StealthChanger Shuttle and Backplate to engage cleanly and the OptoTap sensor to detect the presence of the Backplate. Klipper-toolchanger has hardcoded pauses to allow for these things to happen reliably and can not be adjusted by the end user.

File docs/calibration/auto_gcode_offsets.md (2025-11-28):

Automated calibration uses specialized tools to measure X/Y/Z offsets more precisely and efficiently. Refer to each tool's documentation for specific calibration procedures.

## Available Methods

{% for method, data in cal_methods.items() %}
{% if method != "Manual" %}
- **[{{ method }}]({{ data.url }}){:target="_blank"}** – {{ data.description }}
{% endif %}
{% endfor %}

## Calibration With SexBall Probe

### Define Switch Location
With the SexBall Probe mounted to the printer's bed extrusion, the absolute position of the ball needs to be added to the [[gcode_macro _CALIBRATION_SWITCH]](#) variables.

``` cfg title="Calibration switch variables example." hl_lines="2 3 4"
  [gcode_macro _CALIBRATION_SWITCH]
  variable_x: 227.471875
  variable_y: 353.703125
  variable_z: 5.00
  gcode:
```

1. Home the printer with `G28`.
2. Run `QUAD_GANTRY_LEVEL` to level the gantry.
3. Home z again with `G28 Z`.
4. Manually move the gantry so that the tool is ~1mm over the ball.
5. Run `M114` to output the current position to console.
6. Enter the positions in to the [[gcode_macro _CALIBRATION_SWITCH]](#) variables.

### Enable Multi Axis Probing
- Enable the multi-axis probe by defining the [[tools_calibrate]](#) section in [toolchanger-config.cfg](#).
- Set the `pin` variable to the pin that your calibration probe is connected to.
- Calibrate `trigger_to_bottom_z`

``` cfg title="[tools_calibrate] example."
  [tools_calibrate]
  pin:   #pin that your calibration probe is connected to.
  travel_speed: 20  # mms to travel sideways for XY probing
  spread: 7  # mms to travel down from top for XY probing
  lower_z: 1.0  # The speed (in mm/sec) to move tools down onto the probe
  speed: 2  # The speed (in mm/sec) to retract between probes
  lift_speed: 4  # Z Lift after probing done, should be greater than any Z variance between tools
  final_lift_z: 6 
  sample_retract_dist:2
  samples_tolerance:0.05
  samples:5
  samples_result: median # median, average
  probe: probe # name of the nozzle probe to use
  trigger_to_bottom_z: 0.25 # Offset from probe trigger to vertical motion bottoms out. 
```

!!! tip "trigger_to_bottom_z"
    `trigger_to_bottom_z` is the travel distance from the point where the nozzle touches the top of the ball to the point where the switch not only triggers, but bottoms out.

    1. Move the gantry so that the nozzle touches the top of the ball.
    2. Using small increments, lower the gantry until you hear the switch trigger.
    3. Run `M114` to log the gantry's current position to the console.
    4. Keep an eye on the tool in the shuttle and continue to lower the gantry. The point where the tool starts to lift in the shuttle is the point where the switch has bottomed out.
    5. Run `M114` again and the difference between the 2 logged values is your `trigger_to_bottom_z` value.

### SexBall Nozzle Calibration

1. Clean all the nozzles of your tools. Any debris on the tool will effect the accuracy of the results.
2. With tool 0 on the shuttle, home the printer with `G28`.
3. Run `QUAD_GANTRY_LEVEL` to level the gantry.
4. Home z again with `G28 Z`.
5. With your hand over the emergency stop, run `CALIBRATE_ALL_OFFSETS`.

!!! info "CALIBRATE_ALL_OFFSETS"
    `CALIBRATE_ALL_OFFSETS` will move the tool over the probe and heat it to 150c before locating the probe. For the first run keep an eye on the printer and make sure the values entered in the config are correct and there isn't a crash.

    After tool 0 has located the probe, it will turn off tool 0's heater and repeat the process for each subsequent tool. Tool 0 will be picked up again once the process has completed.

    The values logged to the console are the offsets to be used in the `[tool Tn]`'s `gcode_x_offset`, `gcode_y_offset` and `gcode_z_offset` variables.

### SexBall Probe Z Offset Calibration

1. Clean the tools nozzle. Any debris on the tool will effect the accuracy of the results.
2. With tool 0 on the shuttle, home the printer with `G28`.
3. Run `QUAD_GANTRY_LEVEL` to level the gantry.
4. Home z again with `G28 Z`.
5. Run `CALIBRATE_NOZZLE_PROBE_OFFSET`.

!!! info "CALIBRATE_NOZZLE_PROBE_OFFSET"
    `CALIBRATE_ALL_OFFSETS` will move the tool over the probe and heat it to 150c before locating the probe. It will then bottom out the probe and use the tool's OptoTap sensor to determine the `[tool_probe Tn]`'s `z_offset`.

    The value logged to the console is the value to be used for the `[tool_probe Tn]`'s `z_offset`.

!!! tip "Don't Trust the Robots"
    The `[tool_probe Tn]` `z_offset` should be verified using a small test print. Because this procedure depends on the accuracy of the `trigger_to_bottom_z` value, it is advisable to confirm the offset by performing a short test print and noting any adjustments required to achieve proper first-layer adhesion.

    - If you need to raise the nozzle during the test print, the `z_offset` must be adjusted closer to zero by the same amount.
    - If you need to lower the nozzle during the test print, the `z_offset` must be adjusted farther from zero by the same amount.

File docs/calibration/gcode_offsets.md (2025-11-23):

# G-code Offset Calibration

## Important Notes
- **Tn refers to the tool on the shuttle** (e.g., T1 = Tool 1).  
- **Only home or probe using T0.**  
- **`gcode_z_offset`, `gcode_x_offset`, `gcode_y_offset` for Tool 0 must always be `0`.** All other tools are offset relative to T0.

!!! warning "Before You Start"
    - All gcode calibration are relative to T0, so it is important that the printer has perfect first layer adhesion with T0 before calibrating the gcode offsets.
    - It is recomended that you run a test print with T0 before calibrating the gcode offsets.

---

## Manual Calibration

Manual calibration uses a paper test to measure Z-offsets between tools.

!!! note "Prerequisites"
    - All tools must have their `z_offset` calibrated first (see [Probe Offset](probe_offset.md))
    - Only home or probe with T0 during this calibration

### GCODE Z Offset Procedure

1. Ensure **T0 is on the shuttle**
2. Run:
    ```gcode
    INITIALIZE_TOOLCHANGER
    ```
3. Home the machine:
    ```gcode
    G28
    ```
4. Level the gantry:
    ```gcode
    QUAD_GANTRY_LEVEL
    ```
5. Home Z again:
    ```gcode
    G28
    ```
6. Raise the nozzle:
    ```gcode
    G1 Z10 F600
    ```
7. **Manually remove the current tool** and place the next tool on the shuttle
8. Perform a [manual paper test](#manual-paper-test) and adjust Z until you feel slight resistance
9. Once satisfied, run `M114` and **copy the Z value**
10. Set this value as `gcode_z_offset` in `[tool Tn]` of the toolhead config file
11. Repeat from **step 6** for all remaining tools
12. Run:
    ```gcode
    FIRMWARE_RESTART
    ```

### Manual Paper Test

The "paper test" involves placing a regular piece of paper between the bed and nozzle, then commanding the nozzle to different Z heights until you feel slight friction when moving the paper.

**Key Points:**
- Use regular copy paper (approximately 100 microns / 0.1mm thick)
- Always perform the test at **room temperature** (both nozzle and bed cold)
- Ensure the nozzle and bed are clean and free of debris
- Use the same surface/tape that you normally print on

**Procedure:**
1. Cut a small piece of paper (approximately 5x3 cm)
2. Place it between the nozzle and bed
3. Using your web interface (Mainsail/Fluidd), jog the nozzle down in small increments
4. Push the paper back and forth to feel for resistance
5. Continue until you feel slight friction (paper can slide but with resistance)
6. Note the Z position using `M114`

---

## Automatic Calibration

Automatic calibration uses specialized tools to measure X/Y/Z offsets more precisely and efficiently.

### Available Methods

- **[Manual Calibration Tool](https://www.printables.com/model/201707-x-y-and-z-calibration-tool-for-idex-dual-extruder){:target="_blank"}** – Print a calibration jig to measure physical distances between nozzles
- **[SexBall Probe](/hardware/calibration_tools/#sexball-probe)** – Mechanical probe using precision spheres for repeatable measurements
- **[Axiscope](https://github.com/nic335/Axiscope){:target="_blank"}** – Camera-based visual alignment to printed targets
- **[NozzleAlign](https://github.com/viesturz/NozzleAlign){:target="_blank"}** – Camera-based alignment system
- **[kTAMV](https://github.com/TypQxQ/kTAMV){:target="_blank"}** – Klipper Tool Alignment Machine Vision
- **[Nudge](https://github.com/zruncho3d/nudge){:target="_blank"}** – Software-guided Mechanical probe

Refer to each tool's documentation for specific calibration procedures.

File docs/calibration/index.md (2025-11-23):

# Calibration Overview

Calibration requires three main steps:

1. [Probe Offset](probe_offset.md)
2. [Dock Positions](dock_positions.md)
3. [G-code Offsets](gcode_offsets.md)

This page is a high-level overview. Use it to understand what needs to be calibrated and where it lives in the config before diving into the step-by-step guides.

---

## 1. [Probe Offset](probe_offset.md)

The first step is establishing a **probe-based Z reference** for each tool.

- **Config section:** `[tool_probe Tn]` in your tool config
- **Parameter:** `z_offset`

### What is `z_offset`?

The `z_offset` is used when the printer homes or levels the bed, it tells Klipper the vertical distance between your probe's trigger point and the nozzle tip.

Klipper uses this offset to calculate where Z=0 is for that specific nozzle.

Each tool could have a different `z_offset` because:

- Assembly tolerances can differ.
- Travel between the nozzle's zero point and the sensor's trigger point can vary

With correct `z_offset` values, consistent first layers are produced.

---

## 2. [Dock Positions](dock_positions.md)

Dock calibration is required for the printer to know where to pick up and park tools in their docks.

- **Config section:** `[tool Tn]` in your tool config
- **Parameters:** `params_park_x`, `params_park_y`, `params_park_z`
### What are park positions?

The park position is the exact X/Y/Z coordinate where the shuttle aligns with a docked tool so they can mechanically couple. Think of it as the "pickup point" for that specific dock.

**Why each tool needs its own park position:**

- Docks are physically mounted at different locations along the front of the printer
- Even small positional errors can cause the shuttle to miss the tool or collide with the dock

With accurate park positions, tool changes become repeatable and collision-free.

---

## 3. [G-code offsets](gcode_offsets.md)

Finally, you align where each nozzle actually prints so that tools agree on Z height and X/Y position on the bed.

- **Config section:** `[tool Tn]`
- **Parameters:** `gcode_z_offset`, `gcode_x_offset`,  `gcode_y_offset`

### What are G-code offsets?

G-code offsets compensate for the physical differences between tools so they all behave as if they're in the same position:

- **`gcode_z_offset`**: Adjusts the effective Z height so all tools produce the same first-layer squish.

- **`gcode_x_offset` and `gcode_y_offset`**: Shift the tool's X/Y position so all nozzles land on the same spot when given identical G-code coordinates. Without these, a multi-tool print would have visible misalignment between layers printed by different tools.

**Why G-code offsets matter:**

When your slicer generates `G1 X100 Y100`, every tool should deposit filament at exactly the same physical location on the bed. G-code offsets make this possible by telling Klipper "this tool is 0.2mm left and 0.1mm forward off the reference tool, so adjust accordingly."

### Calibration Methods

There are several ways to measure these offsets:

- **[Manual](https://www.printables.com/model/201707-x-y-and-z-calibration-tool-for-idex-dual-extruder){:target="_blank"}** - Measuring the physical distance between nozzle with a printed tool
- **[SexBall Probe](/hardware/calibration_tools/#sexball-probe)** – Mechanical probe using precision spheres for repeatable measurements
- **[Axiscope](https://github.com/nic335/Axiscope){:target="_blank"}** – Camera-based visual alignment to printed targets
- **[Nudge](https://github.com/zruncho3d/nudge){:target="_blank"}** – Software-guided Mechanical probe

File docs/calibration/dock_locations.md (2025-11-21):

# Dock Locations & Setup Guide

!!! warning "Important"
    It is important that T0 has a calibrated `z_offset` before calibrating the docks.

!!! warning "Important"
    Don't forget to set you tool path in the config.

## Parameter Definitions

- **params_safe_y**  
  The absolute Y-distance from machine zero to the back of the tools in the dock.  
  This should include extra clearance for safety.

- **params_close_y**  
  The relative distance from `safe_y` that the gantry moves to during tool changes.

- **params_fast_speed**  
  The movement speed used when the toolhead is *outside* the dock during a tool change (mm/min).

- **params_path_speed**  
  The movement speed used for pickup/drop-off while *inside* the dock area (mm/min).

- **params_park_x**  
  The absolute X-position of the tool in its dock.

- **params_park_y**  
  The absolute Y-position of the tool in its dock.

- **params_park_z**  
  The absolute Z-position where the tool and shuttle mate, determined when the TAP (or Z-probe) triggers.

---

## How to Find Dock Locations

Follow this guide to accurately locate each toolhead dock and set the correct parameters in your toolhead configuration.

⚠️ **Warning:** Start slow. Increase speed only after confirming clearances. Crashing into the dock can cause serious damage.

### 1. Prepare the Printer
1. **Home** the machine.  
2. Perform **QGL** (Quad Gantry Leveling).

### 2. Manually Position Tool T0 in Its Dock
1. Using your GUI (Mainsail or Fluidd), carefully move **Tool 0 (T0)** into its dock.  
2. Align the **feet of the backplate** with the **rear of the dock**.

   - The back of each dock is adjustable—this ensures the tool sits flat and pins align properly when the shuttle picks it up.
   - If your toolhead leans or does not mate cleanly, adjust the dock’s rear stop.

### 3. Find the Proper Alignment
1. Once the tool is positioned correctly, **move down slowly** until the pins clear the shuttle.  
2. Move slightly in **positive Y**, then back toward the tool.  
3. Move upward to **pick up the tool**, ensuring the motion is smooth and the tool seats without shifting.

### 4. Confirm a Clean Pickup
- Repeat the motion until you can manually pick up the tool reliably, without wobble or misalignment.

### 5. Record Coordinates
Record the following:

- **X and Y:**  
  The coordinates where the tool sits correctly in the dock.  
  Use these values for `params_park_x` and `params_park_y`.

- **Z:**  
  The height where the **backplate and shuttle fully mate** and the **TAP sensor triggers**.  
  Use this value for `params_park_z`.

### 6. Update the Toolhead Config
- Insert your recorded values into the tool’s config under `params_park_x`, `params_park_y`, and `params_park_z`.

### 7. Repeat for Each Tool
- Perform the same procedure individually for T1, T2, etc.

---

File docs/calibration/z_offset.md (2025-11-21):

{% include "_templates/probe_offset.md" %}

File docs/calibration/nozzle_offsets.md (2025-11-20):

# GCODE Z-Offset Calibration Procedure (Multi-Tool / Toolchanger)

## Important Notes
- **Tn refers to the tool on the shuttle** (e.g., T1 = Tool 1).  
- **Only home or probe using T0.**  
- **`gcode_z_offset` for Tool 0 must always be `0`.** All other tools are offset relative to T0.

---

## 1. Set Z-offsets for all tools
You will measure each tool relative to the bed using a manual paper test.

---

## 2. Prepare the Machine

1. Ensure **T0 is on the shuttle**.  
2. Run:
    ```gcode
    INITIALIZE_TOOLCHANGER
    ```
    - This ensures the toolchanger system is in a known state.  
3. Home the machine using T0:
    ```gcode
    G28
    ```
    - Always use T0 for homing.  
    - After this, the machine knows the absolute positions.  
4. Ensure the bed is clean and free of debris.

---

## 3. Set Z-offset for T0 (reference tool)

1. Load T0 (if not already loaded).  
2. Move the nozzle above the bed (use the center for consistency):
    ```gcode
    G1 X100 Y100 Z10 F6000
    ```
3. Use a sheet of paper to set the Z-offset manually:
    - Lower the nozzle in small increments until the paper can just slide under the nozzle with slight resistance.  
    - Record this position as `Z=0` for T0.  
4. Set the Z-offset for T0 to 0 in Toolprobe section of T0 toolhead config:
 
---

## 4. Measure Gcode_offset for all other tools (T1, T2, …)

> **Important:** All measurements are relative to T0.

1. Load the next tool, e.g., T1:
    ```gcode
    T1
    ```
2. Move to the same X/Y position used for T0:
    ```gcode
    G1 X100 Y100 Z10 F6000
    ```
3. Lower the nozzle until the paper test gives slight resistance.  
4. Record the Z position displayed by the machine (let’s call it `Z_measure`).  
5. Compute the tool offset relative to T0:
    ```
    gcode_z_offset_T1 = Z_measure - Z_T0
    ```
6. Set this offset in The toolhead config:
 
7. Repeat steps 1–6 for all remaining tools.

---

## 5. Verify Offsets

1. Home the machine with T0:
    ```gcode
    G28
    ```
2. Load each tool in turn and move to the same test point:
    ```gcode
    Tn
    G1 X100 Y100 Z5 F6000
    ```
3. Check that the nozzle lightly touches paper at the same Z height. Adjust offsets if necessary.

---

## 6. Final Notes
- Always **home with T0**.  
- Do not change `gcode_z_offset` for T0.  
- Keep a record of all tool offsets for future reference.

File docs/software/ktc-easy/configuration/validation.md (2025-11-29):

!!! failure "Klipper Error"
    If you are experiencing Klipper errors after setting up your toolchanger-config and T0 config, please consult [Software Troubleshooting](../../troubleshooting.md).

## Pre Launch
Before configuring and calibrating the other tools, it is advised to get the printer printing with tool 0 before continuing configuration of everything else. Before homing and starting a print, there are some checks we should do to make sure everything behaves as intended.

### Hardware Checks
Make sure your toolhead passes all of the following checks before continuing.

1. When you place the tool on the shuttle the OptoTap sensor triggers its LED.
2. The part cooling fans turn on with `M106 S127` and off with `M107`.
3. The hotend heats up and the hotend fan turn on with `M104 S200`.
4. Once at temperature, the extruder motor moves with `G1 E100 F100`.
5. Finally, turn the hotend off with `M104 S0`

If any of these steps fails, the issue could be either hardware or software related. Consult the [Hardware Troubleshooting](../../../hardware/troubleshooting.md) and [Software Troubleshooting](../../troubleshooting.md).

### Tool detection and homing
1. Check that the tool detection is working by running `INITIALIZE_TOOLCHANGER` with, and without the tool on the shuttle. You should get confirmation that the tool either was or wasn't detected.
2. With the tool on the shuttle, home the Y axis by running `G28 Y`.
3. Run `G28 X`.
4. Run `G28 Z`.

!!! success
    At this point the printer should be homed and everything is running as intended. 
    
    If you have any issues initializing or homing, please consult [Software Troubleshooting](../../troubleshooting.md).

### Backplate Break In
Because the StealthChanger’s action relies on precisely fitted pins and bushings, it’s a good idea to operate the mechanism repeatedly to allow the components to seat properly. This break-in process should be performed for every tool.

!!! note "TAP Only"
    This method only works for TAP probing.

1. Heatsoak your printer.
2. Run `G28`
3. Run `QUAD_GANTRY_LEVEL`
3. Run `G28 Z`
2. Run `PROBE_ACCURACY SAMPLES=100`

!!! failure "Failure"
    If you experience failure during this step or you feel the accuracy is not as good as it should be, consult the [Hardware Troubleshooting](../../../hardware/troubleshooting.md) section.

{% include "_templates/probe_offset.md" %}

## First Print
If you copied your [extruder] values from a previous config, you are ready for your first print. If your setting up the printer for the first time, you may need to PID tune your hotend and tune your extruder first.

!!! tip "Extruder Tuning"
    For PID tuning we recommend [Voron's PID Tuning Guide](https://docs.vorondesign.com/build/startup/startup.html?model=v2&step=11&interface=mainsail&probe=tap){:target="_blank"}.

    For extruder calibration we recommend [Ellis' Extruder Calibration Guide](https://ellis3dp.com/Print-Tuning-Guide/articles/extruder_calibration.html){:target="_blank"}.

Run a print as you would for any standard printer first print. As long as the tool is on the shuttle, the printer will behave as any other TAP based printer.

!!! question "Is that it?"
    Getting a single tool printing is much the same as any other printer. We shouldnt bother ourselves with any tool offsets or park positions just yet.

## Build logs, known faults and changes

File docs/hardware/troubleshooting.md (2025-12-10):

## Common Issues
### Shuttle and Backplate Resistance
- Measure the outside of your top pins. You should have 39mm.
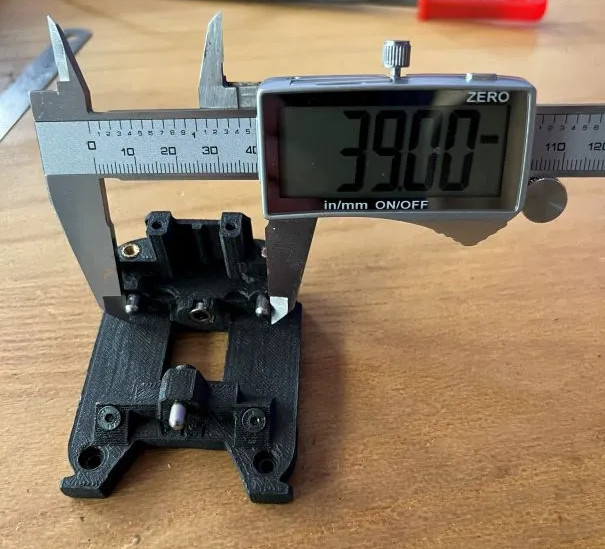
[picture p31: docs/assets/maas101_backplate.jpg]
Pin_Caliper
  

- See [Print Tuning](../getting_started.md#print-tuning)

- If you have calibrated your print and still experience issues, you may want to try the heat treatment method or you can try cleaning out the bushings:

!!! tip "Heat Treating"
    If you printed the shuttle and backplate and things are just not smooth or you have slight binding, you can Heat Treat it and here is how.

    - Fully assemble the shuttle and backplate with Bushing, Pins, Screws and Magnets
    - Set your heat bed to 100-110°C
    - Once at temperature, mate both parts fully, and set them on the bed with the backplate (tool side) down
    - After 20+ minutes pick them up and slide them 3-4 times, then fully mate them once again
    - With both parts still fully mated, set them down with the backplate (tool side) down someplace flat and at room temperature and let them fully cool without touching the for 5+ hours
    - Try and slide them again and you should feel an improvement, you can try this multiple times if you are still not satisfied

    Big thank you to unguided-wanderer on Discord for this technique.

!!! tip "Cleaning Bushings"
    Sometimes the bushings aren't debured or do not slide well when you recieve them.

    - Find a drill bit 4mm or smaller (I’m using 3mm in the video at the link)
    - Using your thumb, apply pressure onto the bush and roll back and forth on the drill bit.
    - Test on the pin again
    - Rinse and repeat.
    - Some bushings take multiple tries, but try not to over do it, just enough that the bushing falls on the pin.

    <iframe width="560" height="315" src="https://www.youtube.com/embed/AHlydBsMJro?si=FXrmA3pIeqSxOLyj" title="YouTube video player" frameborder="0" allow="accelerometer; autoplay; clipboard-write; encrypted-media; gyroscope; picture-in-picture; web-share" referrerpolicy="strict-origin-when-cross-origin" allowfullscreen></iframe>

    Big thank you to BT123 on Discord for this technique.

!!! tip "Last Resort"
    If you can't get the Shuttle and Backplate to mesh cleanly after attempting heat treatment and cleaning the bushings, you can try heating the pins with a soldering iron. This is a last resort and should only be done if you have tried everything else.

    - Heat up the pin with a soldering iron.
    - While the pin is hot, push it into the backplate with pliers (don't burn yourself!)
    - Quickly put the backplate or tool onto the shuttle while the pin is still hot and make sure it seats fully.
    - Wait 5-10min to let it cool down and settle.
    - Tighten the pin with a screw or epoxy it in place.

    Big thank you to Sebastiaan on Discord for this technique.
---

###  Gantry Can't Reach the Bed
Some tools are shorter than others and with some of the shorter tools the z-rail carriages reach the end of their travel before the nozzle can reach the bed, this can be a problem for probing, QGL and printing.

- Remove or modify the Z-belt-covers
- Use taller bed spacers
- Some tools like A4T & XOL require the use of lower profile Z joints. hartk's [GE5C Z Joint](https://github.com/VoronDesign/VoronUsers/tree/main/printer_mods/hartk1213/Voron2.4_GE5C){target="_blank"} or Ellis' [Short Z Joints](https://github.com/VoronDesign/VoronUsers/tree/main/printer_mods/Ellis/Short_Z_Joints){target="_blank"} are good options.

---

### Inconsistant QGL
- Make sure the umbilical cable is not pulling on the toolhead as it probes.
- Check preload screws.

### Bad Input Shaper Results
- Ensure the Backplate's preload screws have been adjusted.
- Check your configuration to ensure the correct accelerometer is assigned to `[resonance_tester]` or the correct accelerometer parameter was specified in the macro. Consult the [Resonance Calibration](../calibration/tuning.md#resonance) section for more information.

---

{% include "_templates/community_help.md" %}

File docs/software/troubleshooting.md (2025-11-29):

## Common Issues
### INITIALIZE_TOOLCHANGER - Tool Not Recognized
- Check that you have the correct pin assigned to the OptoTap sensor.
- If the tool initializes while off the shuttle, the logic is flipped. Either add or remove `!` to the pin definition.
- Some OptoTap sensors require a pullup to operate. Try adding a `^` to the pin definition.
- Check wring/crimps.

---

### INITIALIZE_TOOLCHANGER - Wrong Tool Recognized
- Check the `tool_number` assignment in the [[tool]](ktc-easy/configuration/tool.md#tool) section.

---

### Wrong hotend fan turns on
- Check the `extruder` assignment in the [[heater_fan]](ktc-easy/configuration/tool.md#heater_fan) section.

---

### Wrong part fans turn on
- Check the `fan` assignment in the [[tool]](ktc-easy/configuration/tool.md#tool) section.

---

### Wrong hotend heats up
- Check the `extruder` assignment in the [[tool]](ktc-easy/configuration/tool.md#tool) section.
- Check the `activate_gcode` extruder in the [[tool_probe]](ktc-easy/configuration/tool.md#tool_probe) section.

---

### Wrong extruder moves
- Check the `extruder` assignment in the [[tool]](ktc-easy/configuration/tool.md#tool) section.
- Check the `extruder` name of the [[tmc2209]](ktc-easy/configuration/tool.md#tmc2209) section.

---

{% include "_templates/community_help.md" %}

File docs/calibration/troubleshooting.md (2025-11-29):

Soon

---

{% include "_templates/community_help.md" %}

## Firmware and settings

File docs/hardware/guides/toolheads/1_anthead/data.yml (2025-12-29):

title: Anthead
author: "DraftShift Design"
primary_parts:
  - "Main Body"
  - "Backplate"
  - "Anthead Spacer"
  - "Light Shield"
  - "LED Carrier"
  - "PCB Mount"
  - "LED Solder Jig"
  - "LED Carrier Jig"

accent_parts:
  - "Duct Right"
  - "Duct Left"
  - "NH Cover Shell" 
  - "Nozzle LED Carrier"
  - "Nozzle LED Restraint"
  - "HE Mount"
  - "Grill"
  - "Nozzle LED Carrier Jig"
  - "Nozzle LED Restraint Jig"

summary: >
  This guide will walk you through the assembly of an Anthead for StealthChanger with community usermods.

  !!! tip "Making the best better?"
      The stock Anthead works really well with StealthChanger, however with some small tweaks we can make it even better. 
      This guide introduces some community usermods to make a complete and robust solution for reliable tool changes with StealthChanger.

printed_bom:
  Complete Anthead:
    qty: 1
    urls:
      Link: "https://download-directory.github.io/?url=https://github.com/N3MI-DG/sc-guides/tree/main/Anthead/STL"

  LED Solder Jig:
    qty: 1
    urls:
      Link: "https://download-directory.github.io/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"

hardware_bom:
  M3x6 BHCS Screws:
    qty: 2
  M3x8 BHCS Screws:
    qty: 14
  M3x12 BHCS Screws:
    qty: 5
  M3x14 BHCS Screws:
    qty: 2
  M3x8 SHCS Screws:
    qty: 4
  M3x28 SHCS Screws:
    qty: 2
  M3 Heat Insert:
    qty: 19
  6x3mm N52 Magnets:
    qty: 2
  Voron Revo Hotend:
    qty: 1
  Orbiter 2.x Extruder:
    qty: 1
  Nitehawk36 Toolhead Board:
    qty: 1
  25x10mm Radial Fan:
    qty: 1
  40x10mm Centrifugal/Blower Fan:
    qty: 2
  4x2mm PTFE ~40mm Long:
    qty: 1

resources:
  Anthead Github: https://github.com/PrintersForAnts/AntHead
  TheSin's StealthChanger Backplate & PCB Mount Usermod: https://github.com/DraftShift/StealthChanger/tree/main/UserMods/TheSin-/PCB36_Mount
  Averen's LED Solder Jig: https://github.com/PrintersForAnts/AntHead/tree/main/UserMods/LED_Solder_Fixture
  N3MI's Nitehawk36 Cover, Spacers & Nozzle LEDs: https://github.com/N3MI-DG/sc-guides/tree/main/Anthead

steps:
  - description: "This guide uses a modified StealthChanger backplate which adds rigid mounting for the toolhead board mount. Both of these mods are by TheSin-. Before starting, ensure you have the correct StealthChanger Backplate for this guide. For assembly of the backplate, see the [StealthChanger Backplate Guide](../../backplates/2_anthead/)."
    camera:
      azimuth: 295
      polar: 118
      distance: 42
      pan_x: 0.87
      pan_y: 0.60
    visible: 
      - "Backplate"
      - "Backplate Hardware"

  - description: 'Solder the 3 LEDs using the [LED Solder Fixture](https://github.com/PrintersForAnts/AntHead/tree/main/UserMods/LED_Solder_Fixture){target="_blank"}'
    camera:
      azimuth: 91
      polar: 34
      distance: 22
      pan_x: 11.55
      pan_y: -0.10
    visible: 
      - "Jig LEDs"
      - "LED Pins"
      - "LED Solder Jig"
      - "LED Wires"

  - description: "Insert the nozzle LEDs in to the Nozzle LED Carrier."
    camera:
      azimuth: 91
      polar: 21
      distance: 17
      pan_x: 16.84
      pan_y: 0.59
    visible: 
      - "Jig LEDs"
      - "LED Pins"
      - "LED Wires"
      - "Nozzle LED Carrier Jig"
    focus:
      - "Jig LEDs"
      - "LED Pins"
      - "LED Wires"

  - description: "Fit the Nozzle LED Restraint in to the Nozzle LED Carrier by hooking the tab on the Carrier and pressing the Restraint down until it clips in to the 2 openings."
    camera:
      azimuth: 232
      polar: 76
      distance: 21
      pan_x: -13.39
      pan_y: -2.54
    visible: 
      - "Jig LEDs"
      - "LED Pins"
      - "LED Wires"
      - "Nozzle LED Carrier Jig"
      - "Nozzle LED Restraint Jig"
    focus:
      - "Nozzle LED Restraint Jig"

  - description: "Slide the LED Carrier over the logo LED. Put the LEDs aside for now, they will be used later in the process."
    camera:
      azimuth: 105
      polar: 53
      distance: 22
      pan_x: 11.19
      pan_y: -2.03
    visible: 
      - "Jig LEDs"
      - "LED Carrier Jig"
      - "LED Pins"
      - "LED Wires"
      - "Nozzle LED Carrier Jig"
      - "Nozzle LED Restraint Jig"
    focus:
      - "LED Carrier Jig"

  - description: "Install 7 heat inserts into the Main Body. Drill out the filament path in the middle with a 4 mm drill for the PTFE tube."
    camera:
      azimuth: 214
      polar: 47
      distance: 28
      pan_x: 0.30
      pan_y: 0.92
    visible: 
      - "Main Body"
      - "Main Body Heat Inserts"
    focus: 
      - "Main Body Heat Inserts"

  - description: "Install 2 heat inserts into the each of the PCB Mount Spacers."
    camera:
      azimuth: 265
      polar: 136
      distance: 23
      pan_x: -0.02
      pan_y: 0.44
    visible: 
      - "Spacers"
      - "Spacer Heat Inserts"
    focus: 
      - "Spacer Heat Inserts"
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

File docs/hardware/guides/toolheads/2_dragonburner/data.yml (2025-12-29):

title: DragonBurner
author: "DraftShift Design"
primary_parts:
  - "Sherpa Mini Mount"
  - "DragonBurner Spacer"
  - "2510 Spacer"
  - "Bambu Mount"
  - "EBB Mount"
  - "Sherpa Mini Printed"
  - "NeoPixel Mount"
  - "Neopixel Carrier"

accent_parts:
  - "Cowl"
  - "DragonBurner Backplate"
  - "Solder Jig"

summary: >
  This guide will walk you through the assembly of an DragonBurner for StealthChanger.

  !!! tip "It's your choice"
      This guide uses the Sherpa Mini extruder, Bambulab Hotend and EBB36 toolhead PCB. You can sway from this configuration if you like, but the hardware BOM may change.

printed_bom:
  Complete DragonBurner:
    qty: 1
    urls:
      Link: "https://download-directory.github.io/?url=https://github.com/N3MI-DG/sc-guides/tree/main/DragonBurner/STL"

hardware_bom:
  M3x8 BHCS Screws:
    qty: 2
  M3x12 BHCS Screws:
    qty: 2
  M3x16 BHCS Screws:
    qty: 2
  M3x20 BHCS Screws:
    qty: 2
  M3x10 SHCS Screws:
    qty: 1
  M3x20 SHCS Screws:
    qty: 4
  M3x40 SHCS Screws:
    qty: 2
  M3 Heat Insert:
    qty: 8
  M3 Nut:
    qty: 1
  5x2mm N52 Magnets:
    qty: 2
  6x3mm N52 Magnets:
    qty: 2
  Bambulab Hotend:
    qty: 1
  Sherpa Mini Extruder:
    qty: 1
  EBB36 Toolhead Board:
    qty: 1
  25x10mm or 30x10mm Radial Fan:
    qty: 1
  40x10mm Centrifugal/Blower Fan:
    qty: 2
  4x2mm PTFE ~29.5mm Long:
    qty: 1

resources:
  DragonBurner Github: https://github.com/chirpy2605/voron/tree/main/V0/Dragon_Burner
  Sherpa Mini Github: https://github.com/Annex-Engineering/Sherpa_Mini-Extruder
  N3MI's CAD and STL collection: https://github.com/N3MI-DG/sc-guides/tree/main/DragonBurner

steps:
  - description: "This guide will walk you through the assembly of a DragonBurner toolhead for StealthChanger."
    camera:
      azimuth: 111
      polar: 81
      distance: 82
      pan_x: -2.66
      pan_y: -1.33
    visible: 
      - "2510 Axial Fan"
      - "2510 Spacer"
      - "4010 Blower Fans"
      - "5x2mm N52 Magnets"
      - "Backplate Hardware"
      - "Bambu Mount"
      - "Bambulab Hotend"
      - "Cowl"
      - "Diffuser"
      - "DragonBurner Backplate"
      - "DragonBurner Spacer"
      - "EBB Mount"
      - "EBB36 PCB"
      - "EBB36 Standoffs"
      - "Heat Inserts (Bambu Mount)"
      - "Heat Inserts (Cowl)"
      - "M3 Nut"
      - "M3x10 SHCS (Spacer)"
      - "M3x12 BHCS Screws (EBB36)"
      - "M3x16 BHCS Screws (Sherpa)"
      - "M3x20 BHCS Screws (Sherpa)"
      - "M3x20 SHCS Screws (Hotend)"
      - "M3x20 SHCS Screws (Sherpa Mount)"
      - "M3x40 SHCS Screws (Cowl)"
      - "M3x8 BHCS Screws (Backplate)"
      - "NeoPixel Mount"
      - "Neopixel Carrier"
      - "PTFE Tube"
      - "Sherpa Mini Hardware"
      - "Sherpa Mini Mount"
      - "Sherpa Mini Printed"
      - "Supports (Bambu Mount)"
      - "WS2812B LED (Logo)"
      - "WS2812B LEDs (Nozzle)"

  - description: 'Solder the 3 LEDs using the [Solder Jig](https://github.com/N3MI-DG/sc-guides/blob/main/DragonBurner/STL/Solder%20Jig.stl){target="_blank"}'
    camera:
      azimuth: 94
      polar: 18
      distance: 40
      pan_x: 0.80
      pan_y: -1.24
    visible: 
      - "Solder Jig"
      - "WS2812B LEDs (Jig)"
    focus:
      - "WS2812B LEDs (Jig)"

  - description: "Insert the LEDs into the NeoPixel Mount. Secure with glue if required."
    camera:
      azimuth: 95
      polar: 84
      distance: 23
      pan_x: 0.78
      pan_y: -0.50
    visible: 
      - "NeoPixel Mount"
      - "WS2812B LEDs (Nozzle)"
    focus:
      - "WS2812B LEDs (Nozzle)"

  - description: "Install the 4 heat inserts in to the Cowl."
    camera:
      azimuth: 276
      polar: 87
      distance: 35
      pan_x: -0.78
      pan_y: -0.49
    visible: 
      - "Cowl"
      - "Heat Inserts (Cowl)"
    focus:
      - "Heat Inserts (Cowl)"

  - description: "Remove the built-in supports from the Bambu Mount."
    camera:
      azimuth: 54
      polar: 141
      distance: 25
      pan_x: -0.36
      pan_y: 1.12
    visible: 
      - "Bambu Mount"
      - "Supports (Bambu Mount)"
    focus:
      - "Supports (Bambu Mount)"

  - description: "Install the 4 heat inserts in to the Bambu Mount."
    camera:
      azimuth: 54
      polar: 141
      distance: 25
      pan_x: -0.36
      pan_y: 1.12
    visible: 
      - "Bambu Mount"
      - "Heat Inserts (Bambu Mount)"
    focus:
      - "Heat Inserts (Bambu Mount)"

  - description: "Install the Hotend in to the Bambu Mount using 2 M3x20 SHCS screws."
    camera:
      azimuth: 149
      polar: 84
      distance: 36
      pan_x: -0.10
      pan_y: 1.19
    visible: 
      - "Bambu Mount"
      - "Heat Inserts (Bambu Mount)"
      - "M3x20 SHCS Screws (Hotend)"
      - "Bambulab Hotend"
    focus:
      - "M3x20 SHCS Screws (Hotend)"
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

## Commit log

2025-11-04 Updated some grammer and added a back plate image.
2025-11-09 Dock Assembly build guide added
2025-11-11 Initial Comit to klipper-toolchanger.md
2025-11-14 add some template content ( print start )
2025-11-14 Fix all the link errors in terminal
    [data.yml, tool_boards.yml]
2025-11-15 Fix Heat Inset in Printed Shuttle Model
2025-11-15 Fix Fanny Pack URLs
    [data.yml]
2025-11-15 Update Fanny PAck Install Printed BOM
2025-11-15 Remove TODO from Umbilical Plate Guide
2025-11-16 Fix images and update Anthead
    [data.yml]
2025-11-18 Change tool and distro boards to cards.
2025-11-20 nozzle offset
2025-11-21 Added some more pages and shuffled some things around
    [Axiscope_Camera.step]
2025-11-21 Make probe offset section a template
2025-11-21 calibration overview initial comit
2025-11-21 Update guides to be self contained
    [Axiscope_Camera.step]
2025-11-21 Update power requirements
2025-11-22 Complete Anthead Assembly
2025-11-22 update calibration overview
2025-11-23 Update Umbilical Assembly
2025-11-26 add tip for accel_chip to specify accelerometer
2025-11-28 add full stealthchanger assembly as guide
2025-11-28 Give calibration code blocks titles
2025-11-29 Add step files for build guides
    [Axiscope_Camera.step, Base - A4T.step, Base - Anthead.step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]
2025-11-29 Multiple grammar corrections and random fixes.
    [data.yml]
2025-12-04 fix 250 assembly image and glb artifacts, fix vscode devcontainer requirements.txt, new
    [data.yml]
2025-12-06 Update link in Anthead guide for backplate assembly
    Fix a broken hyperlink in the AntHead guide.
    [data.yml]
2025-12-07 Add provision for extra comments in toolhead section.
2025-12-08 Add maximize button and use url params for steps.
2025-12-10 Reduce data.yml typos
    Reviewed the build guide by following it. Fixing typos mostly, but adding a few notes for clarity. Not reordering any steps tonight
    [data.yml]
2025-12-10 Machine Screw Counts
    Our friend the captive M3x12 BHCS/SHCS
    Updated BOM counts from the count used in the guide
2025-12-10 Add a picture of the 39mm pins
    Thanks to maas101 (robinmalpas3737) on the discord for allowing us
    to use his photo to improve the documentation
2025-12-13 Hightlight Anthead Spacer
2025-12-13 Specify which dock gets which screws.
2025-12-13 Specify screws for stubby/standard depths
2025-12-18 Improve layout for small devices
2025-12-20 Add endstop_pin virutal endstop info
2025-12-21 added clarification to 48V PSU option
2025-12-21 clarifying the content of umbilical cables
2025-12-21 added explanation for the need of calibration
2025-12-21 small typos and grammar fixes
    [data.yml]
2025-12-24 Specify 13mm pins for LDO CNC Shuttle.
2025-12-24 Explicitly show the spacer for Backplates that need it.
2025-12-29 Ensure we always reset focus when switching steps.
2025-12-29 hint to drill filament path on Anthead added
2025-12-29 typos / grammar in Anthead Backplate guide fixed
    [data.yml]
2025-12-29 added references to print_start/end for existing config
2025-12-29 PRINT_START example, use set TOOL parameter consistently
